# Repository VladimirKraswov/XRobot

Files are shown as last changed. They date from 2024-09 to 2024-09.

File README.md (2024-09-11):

# Dummy-Robot: Super Compact Smart Robotic Arm
> **My super compact robotic arm project.**
>
> Video Introduction: [【Homemade】I Made a Steel Iron Man Robotic Arm!【Hardcore】](https://www.bilibili.com/video/BV12341117rG)
>
> Video: [I made a DUMMY ROBOTIC ARM from scratch! - YouTube](https://www.youtube.com/watch?v=F29vrvUwqS4)





### Documentation (Updated on 22-2-9)

- Добавлены исходные файлы дизайна 3D-моделей.
- Добавлены файлы аппаратного дизайна захвата и печатной платы светодиодного кольца.
- Добавлены файлы печатной платы для беспроводного контроллера пространственного позиционирования.
- Добавлены программное и аппаратное обеспечение для беспроводного устройства обучения Peak (в виде подмодуля).
- Добавлены файлы аппаратного дизайна REF.
- Добавлено настольное приложение DummyStudio.
- Добавлен исходный код прошивки для основного контроллера Dummy (см. инструкции ниже).
- Добавлен проект аппаратной части для шагового двигателя на 42 шага.
- Добавлен проект аппаратной части для шагового двигателя на 20 шагов.
- Добавлен исходный код прошивки для шаговых двигателей на 42/20 шагов.
- Добавлен инструмент командной строки "reftool" (на основе фреймворка odrivetool).
- Добавлены файлы модели для портативного переносного кейса.

> Это полное решение для оригинального роботизированного манипулятора, показанного в видео. Стоимость и сложность этого варианта довольно высоки, поэтому я рекомендую дождаться выхода **молодежной версии Dummy**, если вы хотите его воспроизвести. Молодежная версия будет включать следующие улучшения:

1. Общая конструкция будет переработана с использованием 3D-печати в качестве производственного решения (в оригинальной версии используется алюминиевое ЧПУ), что значительно снизит затраты на производство.
2. Будет использоваться мой собственный компактный циклоидальный редуктор вместо оригинального гармонического привода, что значительно снизит стоимость компонентов.
3. Всё программное и аппаратное обеспечение будут совместимы и сохранят ту же функциональность, что и в оригинальной версии.
4. Будет включено приложение для ПК и мобильное приложение (с руководством по первоначальной настройке для пользователей), разработанные мною.
5. Метод подключения оригинального привода двигателя будет улучшен. В оригинальной версии для подключения питания использовалась пайка, что неудобно для установки и демонтажа. В молодежной версии будет использоваться 4-контактный разъем (питание + шина CAN).
6. Общая стоимость будет стремиться оставаться ниже 2000 единиц.
7. **И самое главное, будет полноценное видео-руководство!**

## О конструктивной части

Оригинальная конструкция, показанная в видео, использует шаговые двигатели и гармонический редуктор. Последний является довольно дорогим компонентом (я купил б/у примерно за 600 единиц), поэтому, чтобы сделать проект более доступным для всех, я позже добавлю бюджетное решение с использованием самодельного циклоидального редуктора и 3D-печати.

> Циклоидальный редуктор уже разработан и в настоящее время проходит тестирование. Ожидается, что он будет изготовлен с помощью резки из поликарбоната (или акрила) в сочетании с 3D-печатью, что приведет к небольшому снижению точности, но сохранит всю функциональность. Ожидается, что стоимость всего оборудования будет удерживаться в пределах 2000 единиц.

Разработанный циклоидальный редуктор можно найти в моем другом репозитории: [peng-zhihui/CycloidAcuratorNano](https://github.com/peng-zhihui/CycloidAcuratorNano).



## О модулях схемы

Для реализации основной функции управления движением роботизированного манипулятора схема состоит из четырёх основных плат:

- Основная плата REF
- Плата основания REF (контроллер внутри основания манипулятора)
- Привод шагового двигателя
- Устройство обучения Peak

Я опубликовал в открытый доступ первые две платы и Peak. При проектировании привода шагового двигателя я ориентировался на проект [unlir/XDrive](https://github.com/unlir/XDrive), разработанный моим другом. Это драйвер с замкнутым контуром на базе STM32, доступный в открытой и закрытой версиях. Закрытая версия использует высокопроизводительные дискретные MOSFET и имеет полную функциональность, в то время как открытая версия использует АЦП и чип управления по схеме отсечки, предоставляя базовые функции без поддержки CAN-протокола.

Я переработал схему печатной платы привода (добавлены файлы для двигателей на 20, 42 и 57 шагов для возможных расширений) и добавил аппаратную поддержку шины CAN. Также я полностью переписал оригинальный код, **предоставив предварительно скомпилированные бинарные файлы, которые можно прошивать напрямую**.



**Основные улучшения следующие:**

1. Код был переписан с использованием C++11, что добавило множество современных возможностей языка. Нижний уровень по-прежнему использует C, что сохраняет высокую производительность кода.
2. Аппаратная зависимость полностью разделена, что упрощает портирование на другие платформы микроконтроллеров в будущем. Убран избыточный код, структура стала более организованной.
3. Добавлены пользовательские шаблоны для протоколов CAN и UART.
4. Добавлено хранение параметров с использованием аналоговой EEPROM, что позволяет сохранять данные при отключении питания.
5. Любое положение может быть установлено как нулевая точка отсчета, что обеспечивает калибровку в пределах полуворота в обоих направлениях (а не только в одном).
6. Полная совместимость с библиотекой STM32-HAL, что позволяет использовать STM32CubeMX для генерации конфигурационного кода.
7. Другие улучшения. Для дальнейшей разработки сосредоточьтесь на файлах в папке "UserApp".

Использование драйвера **Ctrl-Step** довольно простое. После загрузки прошивки при первом включении двигатель выполнит калибровку энкодера. Если она успешна, при последующих включениях нажатие кнопки 1 переведет систему в режим замкнутого контура, и двигатель можно будет управлять, отправляя команды через CAN или UART. Инструкции можно найти в исходном коде в папке "UserApp", особенно в файлах "interface_can.cpp" и "interface_uart.cpp".



### Другие функции кнопок:

- **Одновременное нажатие обеих кнопок при включении** запускает автоматическую калибровку энкодера. Если первоначальная калибровка не удалась, её можно повторить таким образом.
- **Кратковременное нажатие кнопки 1** переключает между режимами **включения/отключения замкнутого контура**.
- **Длительное нажатие кнопки 1** перезагружает плату.
- **Кратковременное нажатие кнопки 2** очищает защиту от блокировки двигателя.
- **Длительное нажатие кнопки 2** сбрасывает целевую позицию в ноль (например, если в режиме позиционирования, положение будет сброшено в ноль).

Другие функции можно настроить через код или протоколы связи, такие как установка **нулевой точки**, **параметры PID**, идентификатор узла CAN и различные параметры движения.

### Альтернативное использование драйверов GRBL:

Можно модифицировать и использовать драйверы GRBL для управления этим манипулятором. Однако у GRBL есть недостаток в виде сильной связанности (он предназначен для ЧПУ, а не для роботизированных манипуляторов), а также неэффективный метод подключения (каждое сочленение требует отдельных проводов для «step/dir», что приводит к длинным проводам для последних суставов).

### Преимущество драйвера замкнутого контура:

В отличие от GRBL, использование интегрированного драйвера с замкнутым контуром позволяет соединить все двигатели последовательно через шину CAN, что требует всего четыре провода для подключения (два для питания и два для сигнала CAN). Модель с шиной также позволяет двигателям работать в режимах усилия, скорости, положения и траектории, в то время как импульсный режим поддерживает только положения и траектории, что ограничивает сложное управление.

### Прошивка Peak:

Программное и аппаратное обеспечение для Peak уже опубликовано в открытом доступе. Более подробную информацию можно найти в файле README в папке SubModules.

## О ядре прошивки

Основной функционал прошивки этого манипулятора заключается в расчете кинематической позы. **Я всё еще его упорядочиваю, но позже он будет открыт с лучшей упаковкой**. Прошивка была перенесена с LiteOS на более знакомый FreeRTOS, что упрощает дальнейшую разработку.

### Инструкции по использованию прошивки REF:

Прошивка включает несколько основных модулей:

- **Драйверы BSP**: Управление встроенными аппаратными компонентами, такими как OLED, IMU, светодиоды, динамики, энергонезависимая память и т.д.
- **Сторонние библиотеки**: Включают графическую библиотеку U8G2 и библиотеку сериализации Fibre.
- **Core**: Официальная библиотека HAL от ST.
- **Driver**: Драйвер ARM CMSIS.
- **Middleware**: Пакет поддержки FreeRTOS.
- **Robot**: Основная библиотека для робота, включая различные алгоритмы и драйверы.
- **UserApp**: Верхнеуровневые приложения, позволяющие разрабатывать другие программы на основе предоставленных API.

> OLED-дисплей перенесён из библиотеки Arduino U8G2, что упрощает отображение отладочной информации. Из-за ошибки аппаратного I2C в STM32 использован программный драйвер I2C для экрана, который в тестах показал более высокую частоту кадров по сравнению с аппаратным I2C.

Класс `DummyRobot` определяет всю функциональность манипулятора. Во время инициализации необходимо задать **информацию о драйвере шагового двигателя** и **параметры DH**.


Информация о драйвере включает в себя идентификатор узла CAN, **направление (реверс или нет)**, передаточное число редуктора и **диапазон ограничения движения**.

Значение параметров DH следующее:

- **d (offset)**: Расстояние вдоль оси предыдущего звена.
- **θ (theta)**: Угол вращения вокруг оси текущего звена.
- **r (radius)**: Расстояние от оси текущего звена до следующего.
- **α (alpha)**: Угол между осями двух последовательных звеньев.

Эти параметры используются для описания геометрии и кинематики манипулятора, что позволяет правильно рассчитывать его движение и позы.



Конфигурация роботизированного манипулятора должна соответствовать критерию Пайпера (три соседние оси суставов робота должны пересекаться в одной точке или быть параллельными), чтобы получить аналитические решения. Поэтому вы можете изменить структуру манипулятора на основе Dummy и заменить параметры DH, чтобы адаптировать мой код к вашему собственному дизайну манипулятора.

> **О запоминании положения и калибровке нуля при включении:**
>
> Поскольку положение абсолютного энкодера действительно только в пределах одного оборота, в промышленных манипуляторах обычно используются энкодеры на выходе для получения абсолютного положения. Однако это снижает точность в 30 раз (из-за передаточного числа редуктора). Более разумным подходом является использование "двойных энкодеров" или "энкодера с низким энергопотреблением + батареи". В этом проекте использование двойных энкодеров повлияло бы на компактность конструкции, поэтому я принял более хитрое решение: используя контур управления током двигателя, манипулятор выполняет низкокрутящийся возврат в нулевую точку после включения. При встрече с механическим ограничителем подтверждается грубая нулевая точка (без использования концевых выключателей), а затем точная корректировка нуля выполняется на основе положения однооборотного абсолютного энкодера. Этот метод обеспечивает нулевую точку без погрешностей и практически не зависит от точности изготовления, поскольку находится в пределах диапазона абсолютного энкодера в 12 градусов (360/30).

### **Прошивка Peak:**

Проект Peak основан на проекте X-Track. Более подробную информацию можно найти в репозитории Peak.

## **О настольном приложении:**

Программное моделирование, показанное в видео, основано на RoboDK. Я разработал драйвер для подключения к Dummy (документация представлена в официальных документах; оригинальная версия использовала интерфейс TCP, но я изменил её на использование последовательного интерфейса, совместимого с протоколом Dummy). Однако, поскольку RoboDK является коммерческим программным обеспечением, я также разработал собственное настольное приложение с использованием Unity3D, которое уже выпущено в репозитории.

Пока нет планов открывать исходный код настольного приложения, так как оно требует еще многих доработок. Моя цель — создать универсальное программное обеспечение, подобное RoboDK, которое можно будет использовать для самодельных роботизированных манипуляторов в будущем. Конечно, это программное обеспечение будет бесплатным.

## **Об алгоритмах управления:**

Кинематика уже реализована. Вычисления прямой и обратной кинематики основаны на традиционных параметрах DH. Прямая кинематика (углы сочленений к позе захвата) довольно проста и имеет уникальное решение. Однако обратная кинематика (поза захвата к углам сочленений) может иметь несколько решений (в общем случае 8). В моей реализации я выбираю набор углов сочленений с наименьшим максимальным изменением среди 6 углов между предыдущей и целевой позами в качестве решения. Это гарантирует, что манипулятор всегда будет переходить с минимальными угловыми перемещениями.

Далее — преобразование углов сочленений в сигналы привода двигателя. Я использую трапецеидальные кривые ускорения/замедления для планирования скорости и положения. Например, в команде MoveJ при получении команды движения по углу сочленения контроллер рассчитывает разности углов для 6 суставов, выбирает сустав с наибольшим угловым отклонением (обозначенный как θ) и вычисляет время, необходимое для движения θ, исходя из параметра JointSpeed (с учетом ускорения и замедления). Это время используется для расчета ускорения, замедления и максимальной скорости для оставшихся 5 двигателей. Затем все 6 двигателей синхронно перемещаются по рассчитанным параметрам, обеспечивая синхронизацию и плавное движение.

Шесть двигателей подключены через шину CAN. Каждый двигатель получает два идентификационных номера (свой собственный ID и ID 0) для связи (ID 0 используется для вещания и синхронизации). После получения команды движения двигатель сохраняет информацию в теневые регистры и начинает движение при получении сигнала синхронизации, что обеспечивает синхронность двигателей.

Наконец, динамическая часть еще разрабатывается и не полностью реализована. Я настоятельно рекомендую обращаться к книге "Введение в робототехнику" для упомянутых выше кинематических и динамических алгоритмов. Она предоставляет детальные объяснения.

## **Режимы команд:**

Прошивка Dummy поддерживает три различных режима команд (команды могут поступать через USB, последовательный интерфейс или CAN). Каждый режим имеет свои характеристики, как показано в таблице ниже:

| | Instruction Frequency | Instruction Execution | Can Be Interrupted | Pause Between Instructions | Suitable Applications |
| --- | --- | --- | --- | --- | --- |
| SEQ (Sequential) | Random, Low (<5Hz) | Executed in FIFO sequence | No | Yes | Sending a series of key poses, waiting for sequential execution, ensures key point reachability; however, there may be pauses between key points due to deceleration. Suitable for applications such as **visual picking, stacking, etc.** |
| INT (Instant) | Random, No Limit | Instruction Overwrites | Yes | No | Used for real-time control, where new instructions overwrite the ongoing one for immediate response. However, if a series of instructions is sent at once, only the last one will be executed. Suitable for applications such as **motion synchronization**. |
| `ToDo` TRJ (Trajectory Tracking) | Fixed, High (200Hz) | Automatic interpolation, executed at fixed intervals | No | No | Suitable for precise trajectory tracking applications; speed is reduced. Example applications include **3D printing, carving, painting, etc.** |

---

> **Особая благодарность авторам следующих проектов:**
>
> * [unlir/XDrive: шаговый двигатель с многофункциональным интерфейсом и замкнутым контуром управления.](https://github.com/unlir/XDrive)
> * [odriverobotics/ODrive: Высокопроизводительное управление двигателями](https://github.com/odriverobotics/ODrive)
> * [olikraus/u8g2: Библиотека U8glib для монохромных дисплеев, версия 2](https://github.com/olikraus/u8g2)
> * [samuelsadok/fibre: Слой абстракции для создания распределенных систем, которые работают «просто так»](https://github.com/samuelsadok/fibre)

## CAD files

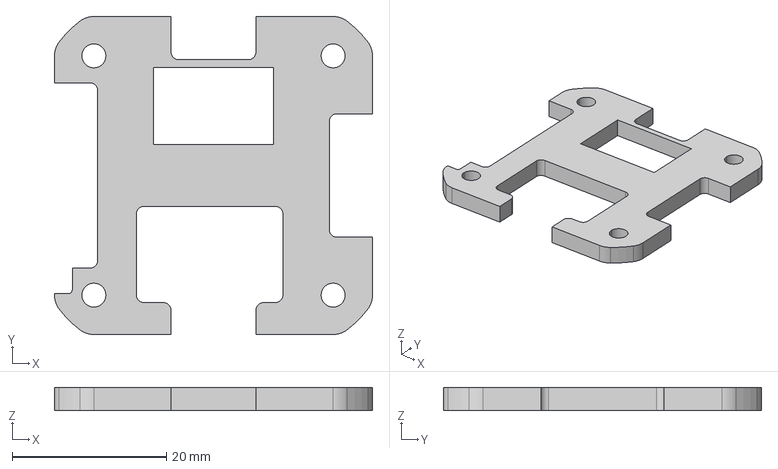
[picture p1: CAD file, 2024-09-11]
4.Model/step/Motor42-X.step
41.2 x 41.2 x 3.00 mm

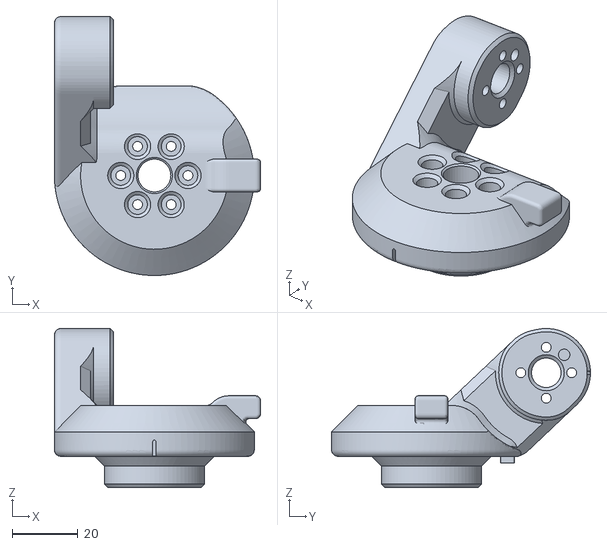
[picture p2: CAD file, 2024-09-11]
4.Model/stl/Join-1.stl
62.9 x 79.0 x 48.5

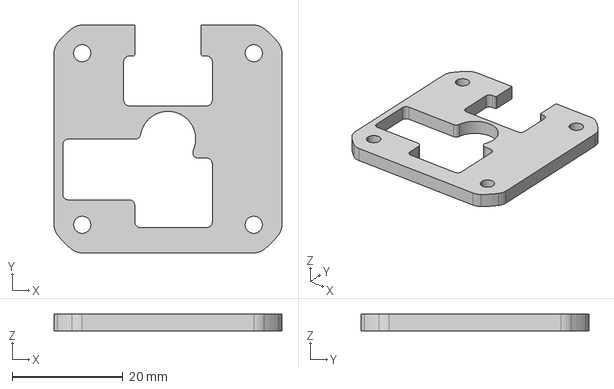
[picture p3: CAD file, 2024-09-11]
4.Model/step/Motor42.step
41.2 x 41.2 x 3.00 mm

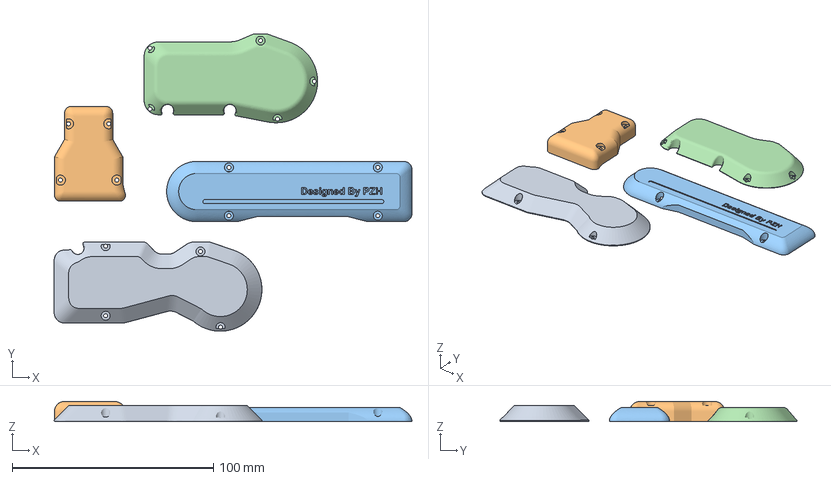
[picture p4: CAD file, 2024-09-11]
4.Model/stl/Join-decors.3mf
178.0 x 147.9 x 10.0 mm
Join-2-1.stl
Join-3-1.stl
Join-5-1.stl
Join-2-2.stl

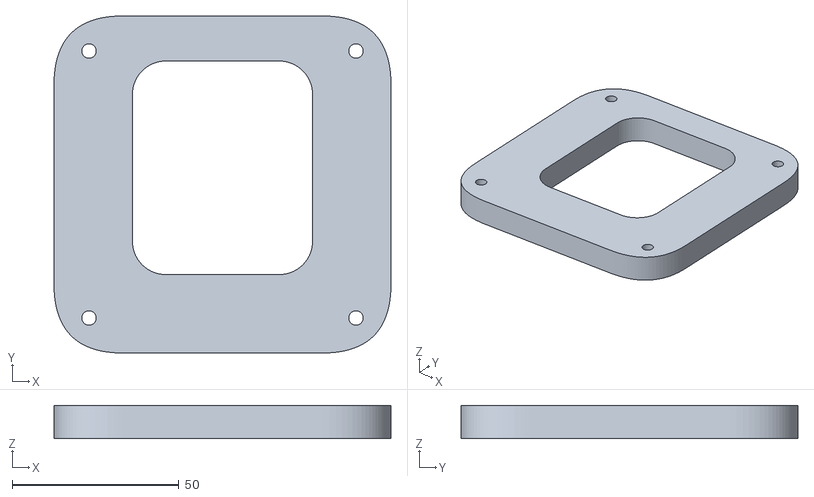
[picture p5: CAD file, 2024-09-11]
4.Model/stl/base-spacer.stl
101.0 x 101.0 x 10.0

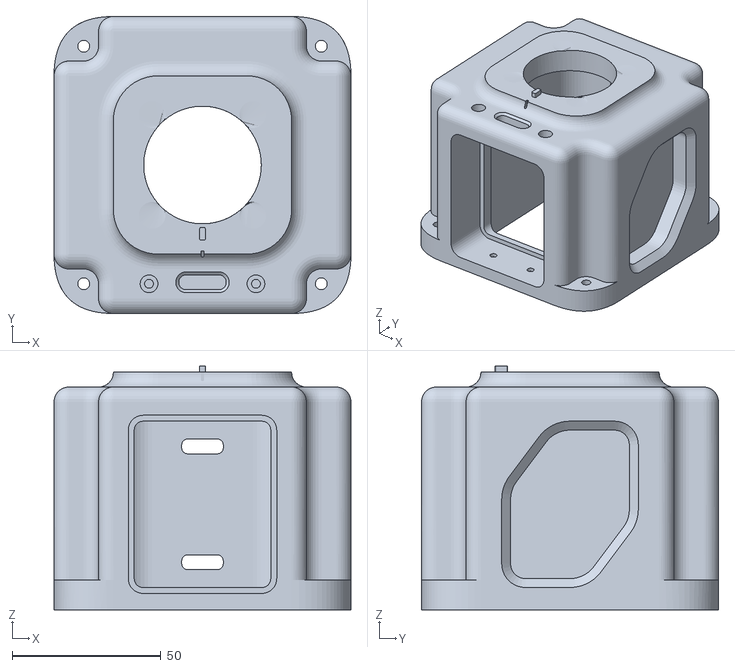
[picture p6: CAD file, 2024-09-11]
4.Model/stl/Base.stl
100.0 x 100.0 x 82.0

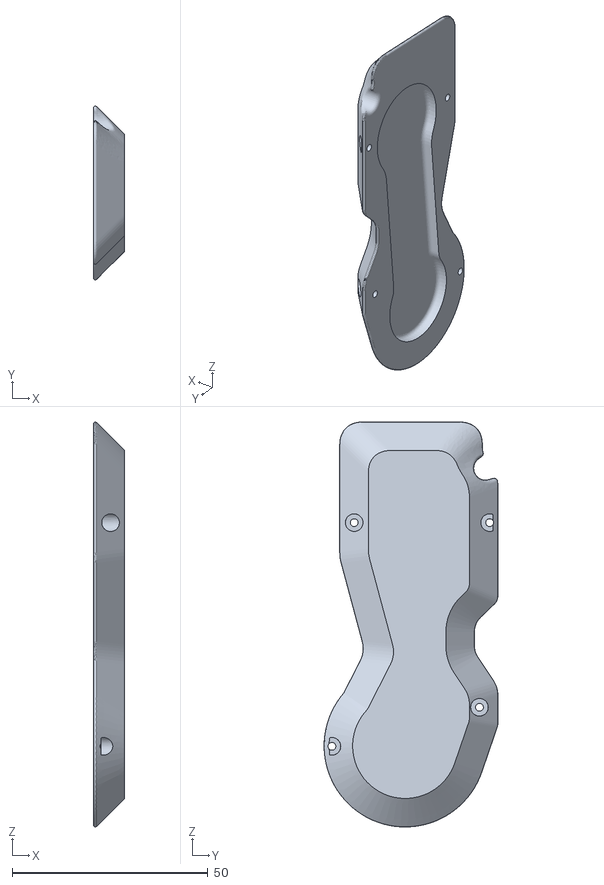
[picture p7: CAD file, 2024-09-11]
4.Model/stl/cover-1.stl
8.00 x 44.4 x 103.4

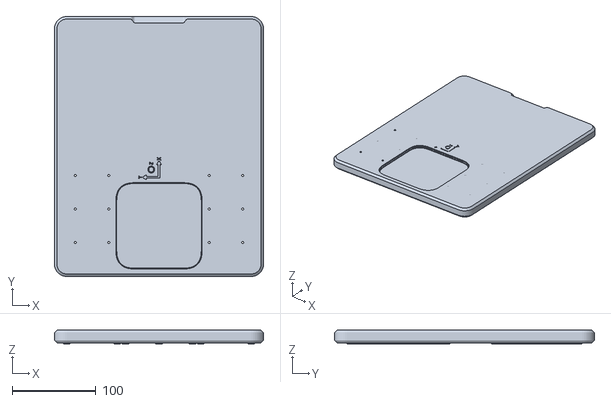
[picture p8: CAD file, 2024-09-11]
4.Model/stl/desktop.stl
250.0 x 310.5 x 16.2

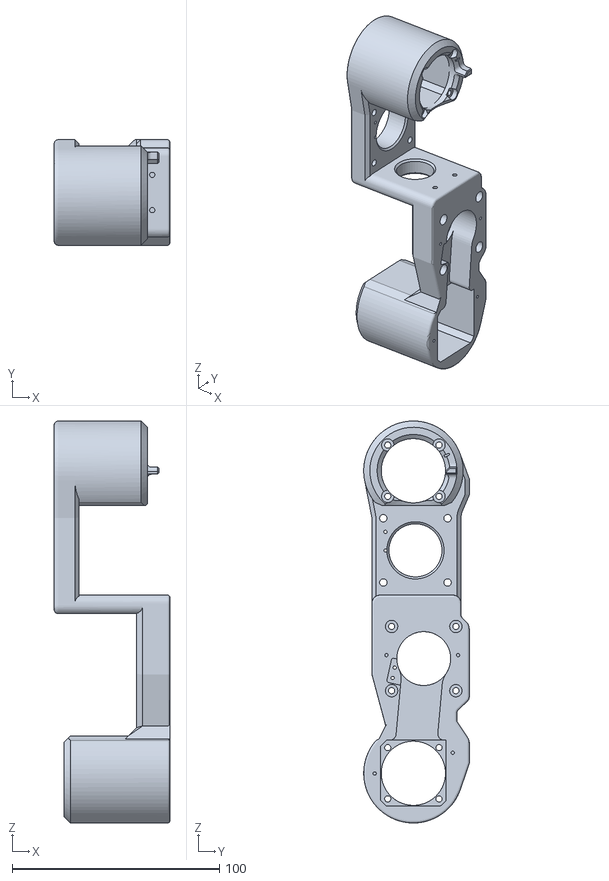
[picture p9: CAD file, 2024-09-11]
4.Model/stl/Join-2.stl
55.9 x 51.0 x 194.0

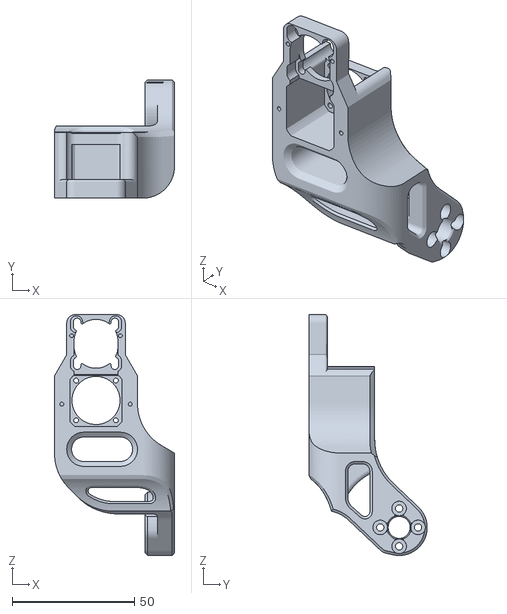
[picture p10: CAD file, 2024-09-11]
4.Model/stl/Join-3.stl
49.1 x 48.5 x 98.7

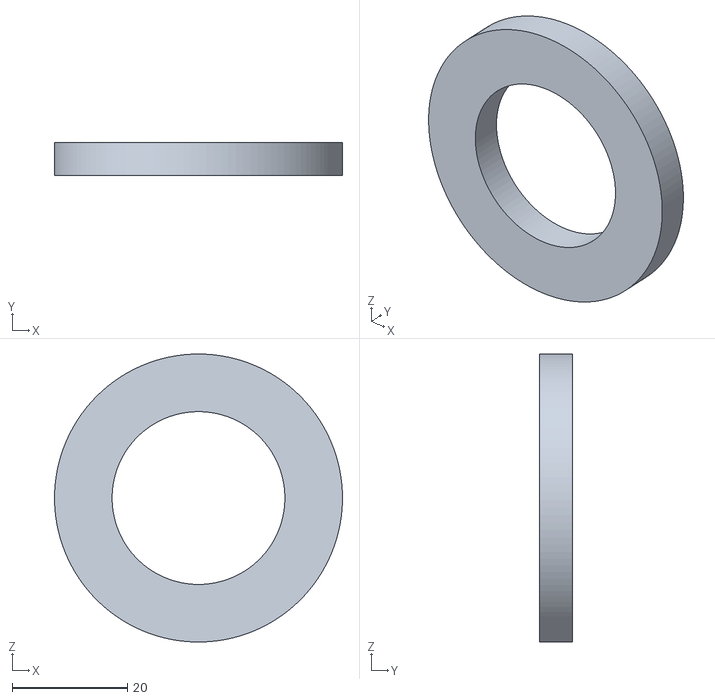
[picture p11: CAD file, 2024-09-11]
4.Model/stl/indicator-light.stl
50.0 x 5.80 x 50.0

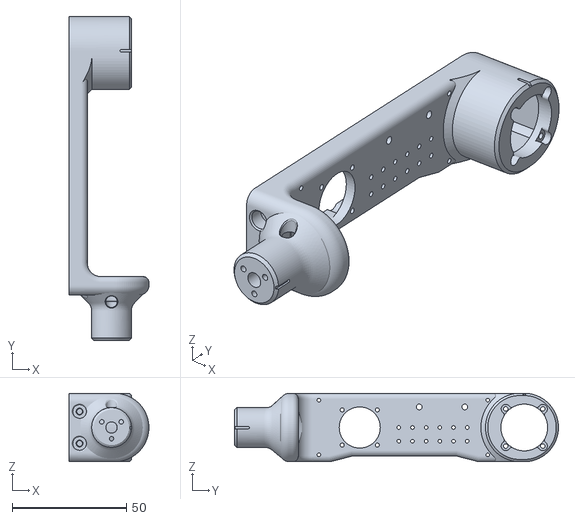
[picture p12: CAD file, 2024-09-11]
4.Model/stl/Join-4.stl
35.0 x 142.0 x 30.0

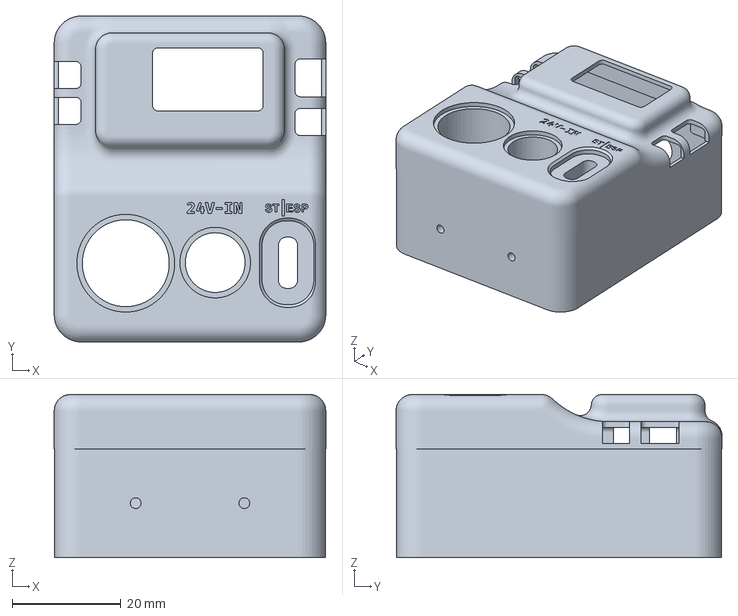
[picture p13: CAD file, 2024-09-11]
4.Model/stl/control-panel.3mf
50.0 x 60.0 x 30.0 mm

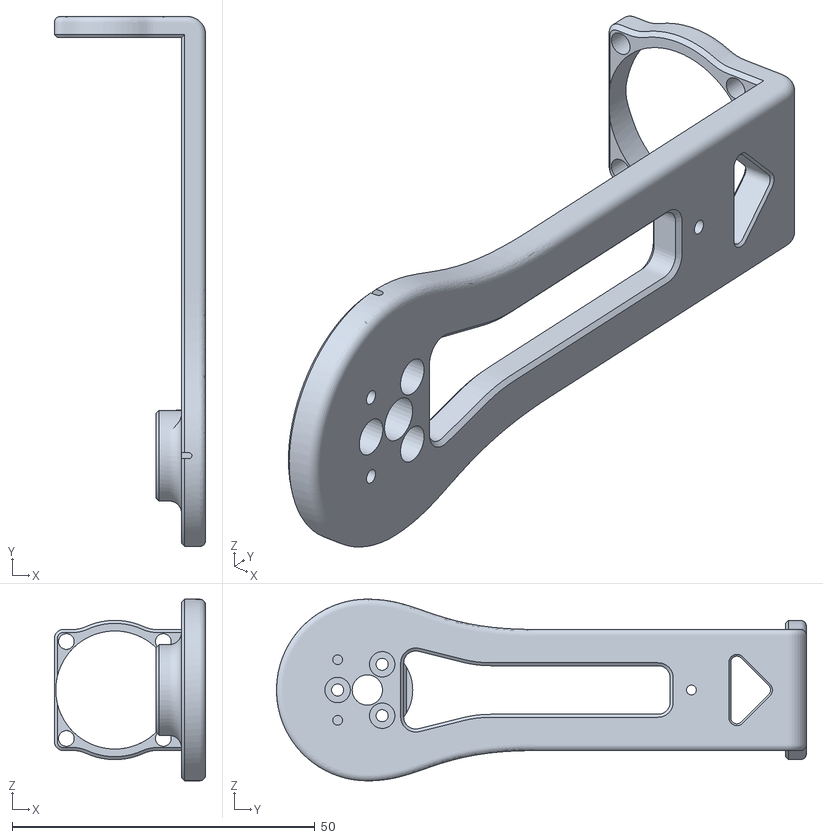
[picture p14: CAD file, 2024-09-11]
4.Model/stl/Join-5.stl
25.0 x 87.5 x 30.0

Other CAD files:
4.Model/stl/cover-4.stl
4.Model/stl/cover-2.stl
4.Model/stl/cover-3.stl
4.Model/freecad/Motor42-X.FCStd
4.Model/freecad/Motor42.FCStd
4.Model/stl/Motor42-X.stl
4.Model/stl/Motor42.stl
4.Model/stl/control-panel.stl
